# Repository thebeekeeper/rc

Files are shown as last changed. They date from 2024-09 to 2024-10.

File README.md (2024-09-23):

TURBO TORNADO
=============

When I was a kid I had a RC car that I really liked to play with, but it pretty rarely worked.  30+ years later I have a couple of decades of experience building embedded systems to control motors and stuff like that so I decided to design replacement electronics for it so my kid can play with it.

To start, I took the top off the car and removed the old PCB.  Here's what we see under there:

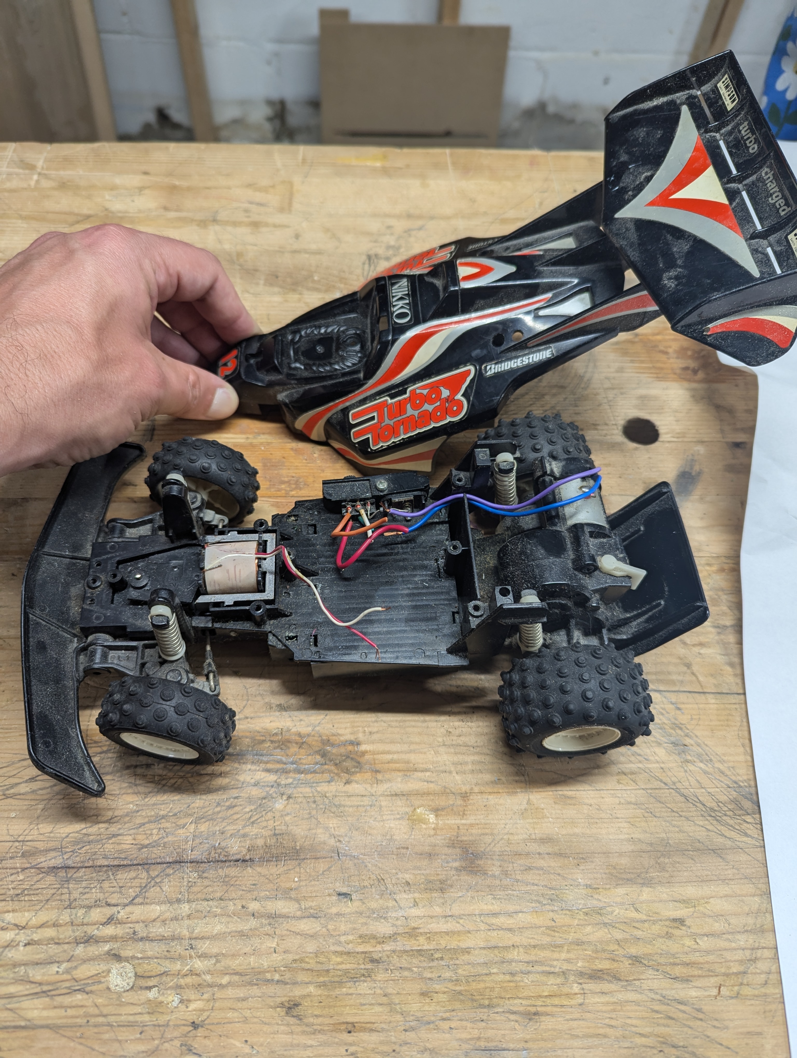
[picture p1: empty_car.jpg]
Empty Car


We've got leads to the coil that controls steering and some on the other end to the drive motor.  On the bottom there are 6 slots for AA batteries, so I'm assuming the motor and solenoid will work off 9V.  I checked this by connecting a 9V battery to both pairs of leads and saw that the steering and drive motor still work.  To change direction of both actuators, you can just reverse polarity on the battery.

What I really want to do with this project is put a camera where that guys head is supposed to be.  I've always wanted a first person view when driving the car around.

## Parts Selection

The features I'm designing for are:

1. Video streaming to some remote device
2. Wireless control
3. Ability to drive two inductive loads with PWM

I've been using `esp32` devices at work for a while, so I decided on the `ESP32-S3-MINI-1U-N8`.  I found the schematic for the `esp32-cam` board [here](https://github.com/SeeedDocument/forum_doc/blob/master/reg/ESP32_CAM_V1.6.pdf) and it looks pretty straightforward to wire to an FPC connector for a standard camera.  It also supports Bluetooth and WiFi, so I'll have some options for wireless control and video streaming.  I've read that it has issues with video quality when using the chip antenna, so I'll plan on using an external antenna.

To drive the motor and solenoid I was initially planning to build couple of standard H-bridge circuits, but then I found [A3909GLNTR](https://www.digikey.com/en/products/detail/allegro-microsystems/A3909GLNTR-T/3979655) which is an IC with the exact circuit I'd be building anyway so I decided to use that.  I've used some Allegro parts in other designs and they've worked well, so this should be pretty easy.

Got the rev0 boards back an assembled and the drive motor just whines and doesn't turn!  Tried adding some capacitance but that didn't really help.  I can't find any specs for the motor that's installed on the machine so I'm guessing the driver IC isn't able to source the stall current for the motor when it's connected to the gearbox.  I tested the driver with a motor I have lying around with no mechanical load on it and it worked fine.  The `A3909GLNTR` datasheet says you can parallel the outputs to get more current.  Tried that and it starts up the motor and runs no problem.  Added a second driver IC and updated the layout for a rev1 board.

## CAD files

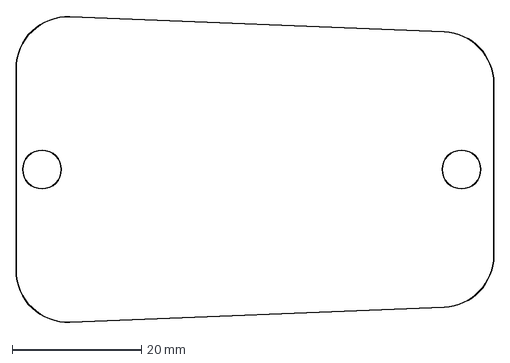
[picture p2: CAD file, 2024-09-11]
board/outline.dxf
74.0 x 47.5 mm

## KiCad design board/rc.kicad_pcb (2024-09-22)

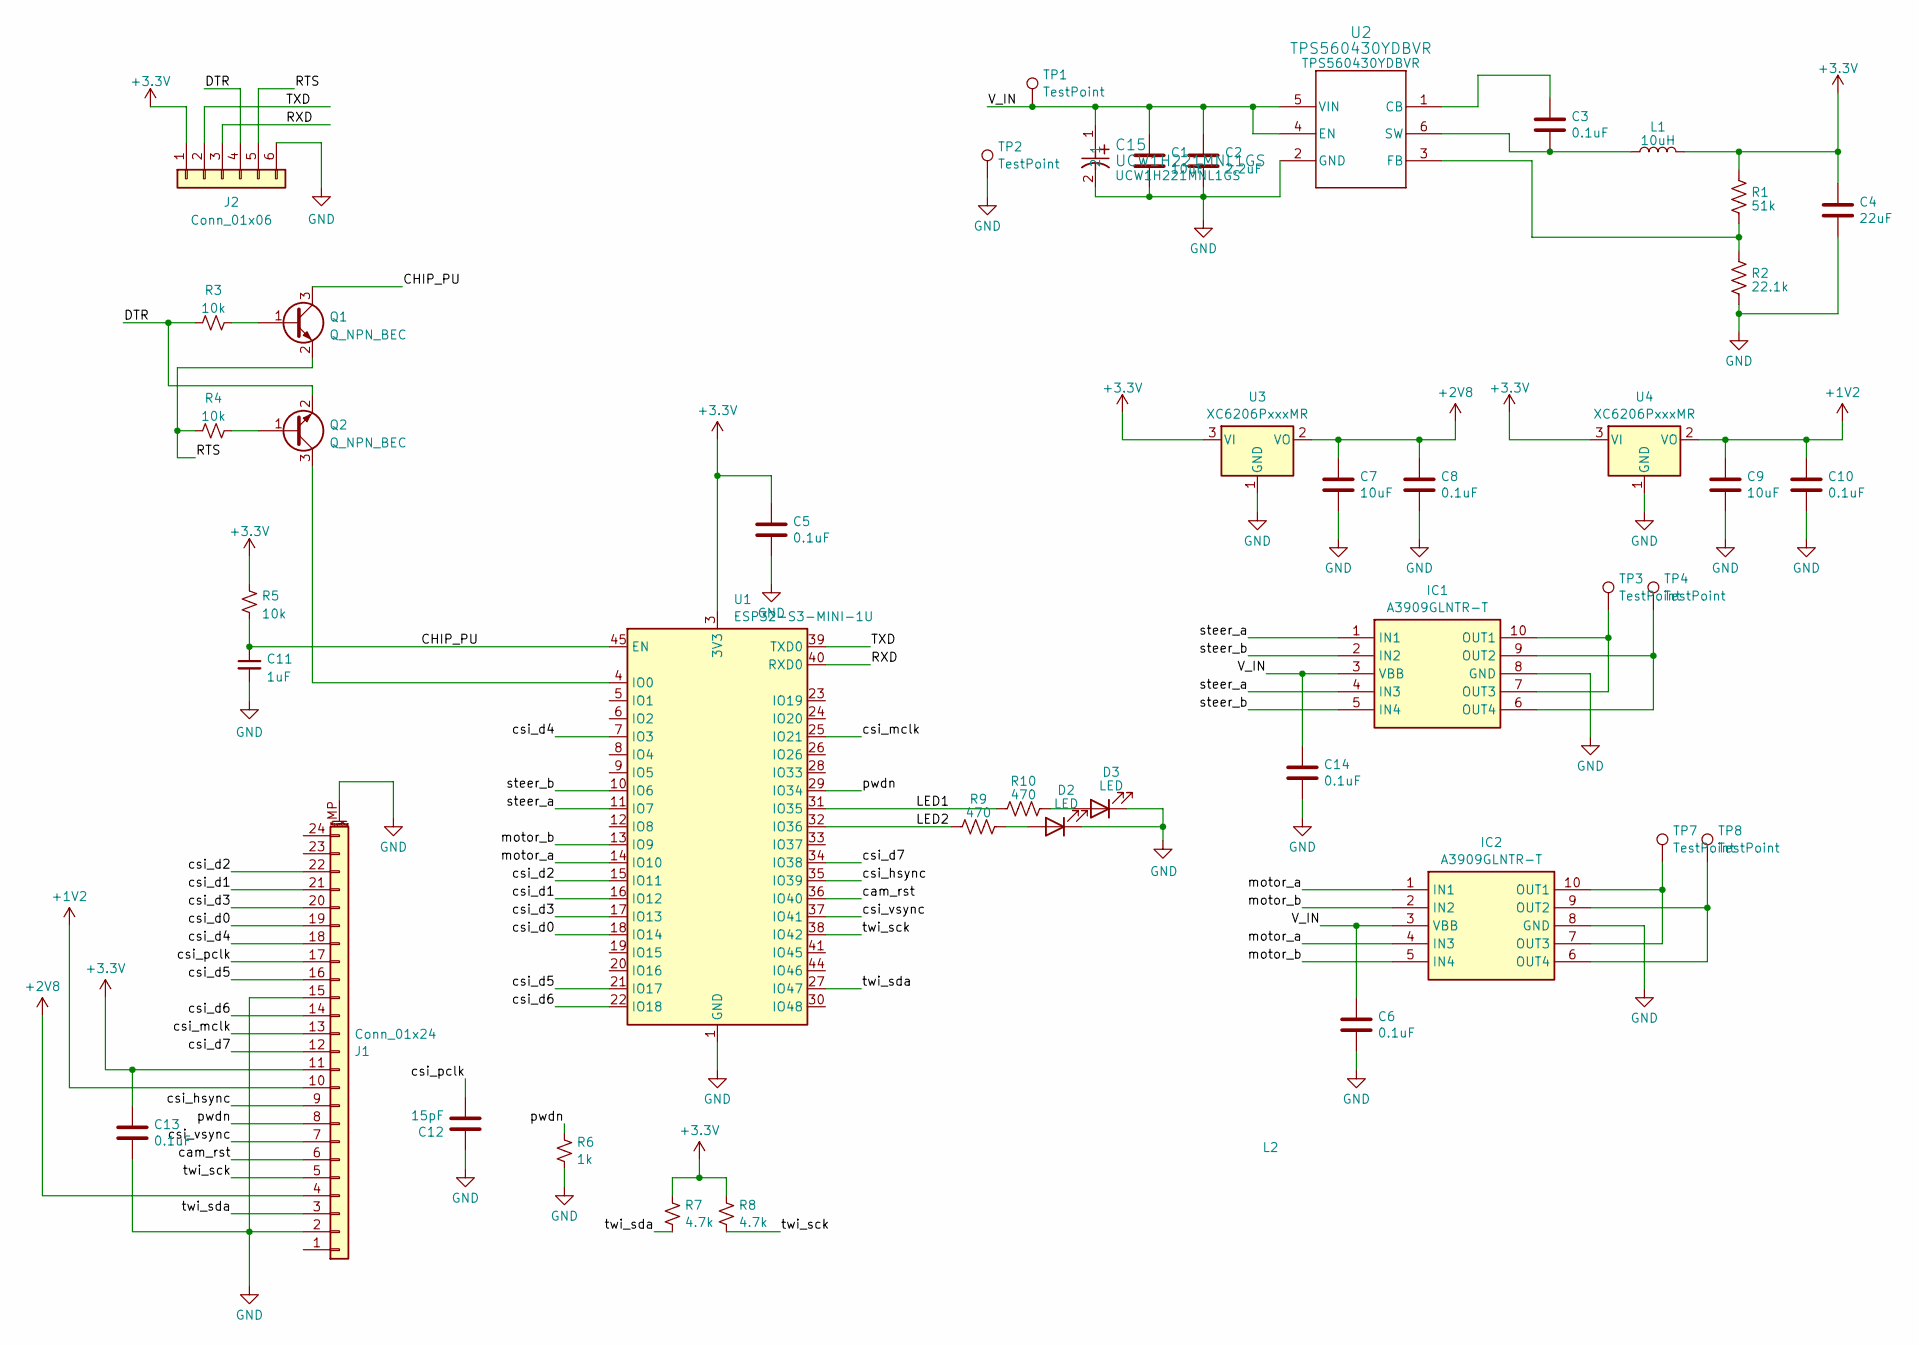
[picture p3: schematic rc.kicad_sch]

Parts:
C1: 10uF; C_1206_3216Metric; ManufacturerPartNumber C3216X5R1H106K160AB
C2: 2.2uF; C_0603_1608Metric; ManufacturerPartNumber GRM188R61H225KE11D
C3, C5, C6, C8, C10, C13, C14: 0.1uF; C_0603_1608Metric; ManufacturerPartNumber GRM188R71H104KA93D
C4: 22uF; C_0805_2012Metric; ManufacturerPartNumber C2012X5R1V226M125AC
C7, C9: 10uF; C_0603_1608Metric; ManufacturerPartNumber GRM188R71H104KA93D
C11: 1uF; C_0805_2012Metric; ManufacturerPartNumber CL21B105KOFNFNE
C12: 15pF; C_0603_1608Metric; ManufacturerPartNumber GRM188R71H104KA93D
C15: UCW1H221MNL1GS; ManufacturerPartNumber UCW1H221MNL1GS
D2, D3: LED; LED_0603_1608Metric; ManufacturerPartNumber B1911USD-20D000114U1930
IC1, IC2: A3909GLNTR-T; SOP100P600X175-10N; Mouser Part Number 250-A3909GLNTR-T
J1: Conn_01x24; Hirose_FH12-24S-0.5SH_1x24-1MP_P0.50mm_Horizontal
J2: Conn_01x06; PinHeader_1x06_P2.54mm_Vertical; ManufacturerPartNumber TSW-106-07-G-S
L1: 10uH; SRN3010C2R2M; ManufacturerPartNumber SRN3010C-100M
L2: bird
Q1, Q2: Q_NPN_BEC; SOT-23; ManufacturerPartNumber MMSS8050-H-TP
R1: 51k; R_0805_2012Metric; ManufacturerPartNumber RMCF0805JT51K0
R2: 22.1k; R_0805_2012Metric; ManufacturerPartNumber RMCF0805FT22K1
R3, R4, R5: 10k; R_0805_2012Metric; ManufacturerPartNumber RMCF0805FT10K0
R6: 1k; R_0805_2012Metric; ManufacturerPartNumber RMCF0805FT10K0
R7, R8: 4.7k; R_0805_2012Metric; ManufacturerPartNumber RMCF0805FT10K0
R9, R10: 470; R_0805_2012Metric; ManufacturerPartNumber RC0805FR-07470RL
TP1, TP2, TP3, TP4, TP7, TP8: TestPoint; MountingHole_2.2mm_M2_ISO7380_Pad_TopBottom
U1: ESP32-S3-MINI-1U; ESP32-S2-MINI-1U
U2: TPS560430YDBVR; DBV0006A_L; ManufacturerPartNumber TPS560430YDBVR
U3, U4: XC6206PxxxMR; SOT-23-3

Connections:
+1V2: C9.1, C10.1, J1.10, U4.2 (VO)
+2V8: C7.1, C8.1, J1.4, U3.2 (VO)
+3.3V: C4.1, C5.1, C13.1, J1.11, J2.1, L1.2, R1.2, R5.1, R7.2, R8.2, U1.3 (3V3), U3.3 (VI), U4.3 (VI)
/CHIP_PU: C11.1, Q1.3 (C), R5.2, U1.45 (EN)
/DTR: J2.4, Q2.2 (E), R3.1
/LED1: R10.1, U1.31 (IO35)
/LED2: R9.1, U1.32 (IO36)
/RTS: J2.5, Q1.2 (E), R4.1
/RXD: J2.3, U1.40 (RXD0)
/TXD: J2.2, U1.39 (TXD0)
/V_IN: C1.1, C2.1, C6.1, C14.1, C15.1, IC1.3 (VBB), IC2.3 (VBB), TP1.1, U2.4 (EN), U2.5 (VIN)
/cam_rst: J1.6, U1.36 (IO40)
/csi_d0: J1.19, U1.18 (IO14)
/csi_d1: J1.21, U1.16 (IO12)
/csi_d2: J1.22, U1.15 (IO11)
/csi_d3: J1.20, U1.17 (IO13)
/csi_d4: J1.18, U1.7 (IO3)
/csi_d5: J1.16, U1.21 (IO17)
/csi_d6: J1.14, U1.22 (IO18)
/csi_d7: J1.12, U1.34 (IO38)
/csi_hsync: J1.9, U1.35 (IO39)
/csi_mclk: J1.13, U1.25 (IO21)
/csi_pclk: C12.2, J1.17
/csi_vsync: J1.7, U1.37 (IO41)
/motor_a: IC2.1 (IN1), IC2.4 (IN3), U1.14 (IO10)
/motor_b: IC2.2 (IN2), IC2.5 (IN4), U1.13 (IO9)
/pwdn: J1.8, R6.2, U1.29 (IO34)
/steer_a: IC1.1 (IN1), IC1.4 (IN3), U1.11 (IO7)
/steer_b: IC1.2 (IN2), IC1.5 (IN4), U1.10 (IO6)
/twi_sck: J1.5, R8.1, U1.38 (IO42)
/twi_sda: J1.3, R7.1, U1.27 (IO47)
GND: C1.2, C2.2, C4.2, C5.2, C6.2, C7.2, C8.2, C9.2, C10.2, C11.2, C12.1, C13.2, C14.2, C15.2, D2.1 (K), D3.1 (K), IC1.8 (GND), IC2.8 (GND), J1.2, J1.15, J1.MP (MountPin), J2.6, R2.1, R6.1, TP2.1, U1.1 (GND), U1.2 (GND), U1.42 (GND), U1.43 (GND), U1.46 (GND), U1.47 (GND), U1.48 (GND), U1.49 (GND), U1.50 (GND), U1.51 (GND), U1.52 (GND), U1.53 (GND), U1.54 (GND), U1.55 (GND), U1.56 (GND), U1.57 (GND), U1.58 (GND), U1.59 (GND), U1.60 (GND), U1.61 (GND), U1.62 (GND), U1.63 (GND), U1.64 (GND), U1.65 (GND), U2.2 (GND), U3.1 (GND), U4.1 (GND)
unnamed: D2.2 (A), R9.2
unnamed: D3.2 (A), R10.2
unnamed: IC1.7 (OUT3), IC1.10 (OUT1), TP3.1
unnamed: IC1.6 (OUT4), IC1.9 (OUT2), TP4.1
unnamed: IC2.7 (OUT3), IC2.10 (OUT1), TP7.1
unnamed: IC2.6 (OUT4), IC2.9 (OUT2), TP8.1
unnamed: Q1.1 (B), R3.2
unnamed: Q2.1 (B), R4.2
unnamed: Q2.3 (C), U1.4 (IO0)
unnamed: C3.1, U2.1 (CB)
unnamed: R1.1, R2.2, U2.3 (FB)
unnamed: C3.2, L1.1, U2.6 (SW)

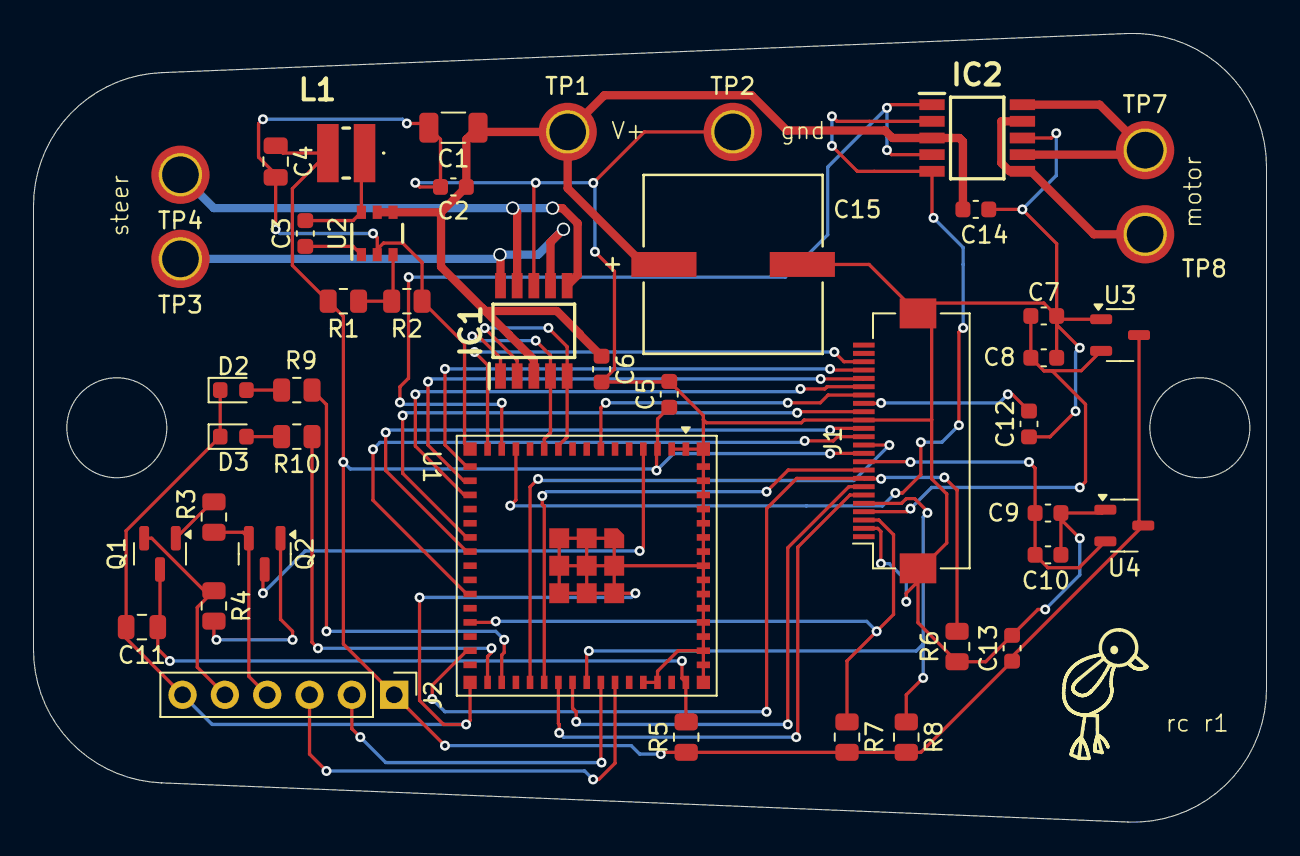
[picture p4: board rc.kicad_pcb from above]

Board: 2 copper layers, 74.0 x 47.3 mm, 45 parts (0 on the bottom side), 44 nets.

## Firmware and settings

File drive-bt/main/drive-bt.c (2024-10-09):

#include <stdio.h>
#include "sdkconfig.h"
#include "freertos/FreeRTOS.h"
#include "freertos/task.h"
#include "esp_system.h"
#include "esp_log.h"
#include "driver/gpio.h"
#include "driver/ledc.h"



#include "nimble/nimble_port.h"
#include "nimble/nimble_port_freertos.h"
#include "host/ble_hs.h"
#include "host/util/util.h"
#include "console/console.h"
#include "services/gap/ble_svc_gap.h"
#include "blecent.h"

#define PWM

#define TAG "drive-bt"

void init_io(void);

#define LED1 GPIO_NUM_35
#define LED2 GPIO_NUM_36

#define STEER_A GPIO_NUM_7
#define STEER_B GPIO_NUM_6
#define MOTOR_A GPIO_NUM_10
#define MOTOR_B GPIO_NUM_9

#define LEDC_TIMER LEDC_TIMER_0
#define LEDC_MODE LEDC_LOW_SPEED_MODE
//#define LEDC_OUTPUT_IO (MOTOR_A) // Define the output GPIO
//#define LEDC_OUTPUT_B (MOTOR_B)
#define MOTOR_A_CHANNEL LEDC_CHANNEL_0
#define MOTOR_B_CHANNEL LEDC_CHANNEL_1
#define STEER_A_CHANNEL LEDC_CHANNEL_2
#define STEER_B_CHANNEL LEDC_CHANNEL_3
#define LEDC_DUTY_RES LEDC_TIMER_13_BIT // Set duty resolution to 13 bits
//#define LEDC_DUTY (1096)                // Set duty to 50%. (2 ** 13) * 50% = 4096
#define LEDC_FREQUENCY (200)            // Frequency in Hertz. Set frequency at 4 kHz

// called from the BLE handler
void update_outputs(int8_t drive, int8_t steer) {
    uint32_t dc = 0;
    if(drive > 10) {
        dc = drive * 53; 
        ESP_LOGI(TAG, "setting drive dc forward: %lu", dc);
        ESP_ERROR_CHECK(ledc_set_duty(LEDC_MODE, MOTOR_A_CHANNEL, dc));
        ESP_ERROR_CHECK(ledc_update_duty(LEDC_MODE, MOTOR_A_CHANNEL));
        // turn off channel B
        ESP_ERROR_CHECK(ledc_set_duty(LEDC_MODE, MOTOR_B_CHANNEL, 0));
        ESP_ERROR_CHECK(ledc_update_duty(LEDC_MODE, MOTOR_B_CHANNEL));
    }
    else if(drive < -10) {
        dc = drive * -53; 
        ESP_LOGI(TAG, "setting drive dc reverse: %lu", dc);
        ESP_ERROR_CHECK(ledc_set_duty(LEDC_MODE, MOTOR_A_CHANNEL, 0));
        ESP_ERROR_CHECK(ledc_update_duty(LEDC_MODE, MOTOR_A_CHANNEL));
        ESP_ERROR_CHECK(ledc_set_duty(LEDC_MODE, MOTOR_B_CHANNEL, dc));
        ESP_ERROR_CHECK(ledc_update_duty(LEDC_MODE, MOTOR_B_CHANNEL));
    }
    else {
        dc = 0;
        ESP_ERROR_CHECK(ledc_set_duty(LEDC_MODE, MOTOR_A_CHANNEL, dc));
        ESP_ERROR_CHECK(ledc_update_duty(LEDC_MODE, MOTOR_A_CHANNEL));
        ESP_ERROR_CHECK(ledc_set_duty(LEDC_MODE, MOTOR_B_CHANNEL, dc));
        ESP_ERROR_CHECK(ledc_update_duty(LEDC_MODE, MOTOR_B_CHANNEL));
    }

    if(steer > 10) {
        //dc = 3000 + (steer * 53); 
        dc = 8192;
        ESP_LOGI(TAG, "setting steer left: %lu", dc);
        ESP_ERROR_CHECK(ledc_set_duty(LEDC_MODE, STEER_A_CHANNEL, dc));
        ESP_ERROR_CHECK(ledc_update_duty(LEDC_MODE, STEER_A_CHANNEL));
        // turn off channel B
        ESP_ERROR_CHECK(ledc_set_duty(LEDC_MODE, STEER_B_CHANNEL, 0));
        ESP_ERROR_CHECK(ledc_update_duty(LEDC_MODE, STEER_B_CHANNEL));
    }
    else if(steer < -10) {
        //dc = steer * 53; 
        dc = 8192;
        ESP_LOGI(TAG, "setting steer right: %lu", dc);
        ESP_ERROR_CHECK(ledc_set_duty(LEDC_MODE, STEER_A_CHANNEL, 0));
        ESP_ERROR_CHECK(ledc_update_duty(LEDC_MODE, STEER_A_CHANNEL));
        ESP_ERROR_CHECK(ledc_set_duty(LEDC_MODE, STEER_B_CHANNEL, dc));
        ESP_ERROR_CHECK(ledc_update_duty(LEDC_MODE, STEER_B_CHANNEL));
    }
    else {
        dc = 0;
        ESP_ERROR_CHECK(ledc_set_duty(LEDC_MODE, STEER_A_CHANNEL, dc));
        ESP_ERROR_CHECK(ledc_update_duty(LEDC_MODE, STEER_A_CHANNEL));
        ESP_ERROR_CHECK(ledc_set_duty(LEDC_MODE, STEER_B_CHANNEL, dc));
        ESP_ERROR_CHECK(ledc_update_duty(LEDC_MODE, STEER_B_CHANNEL));
    }
}


static void example_ledc_init(void)
{
    // Prepare and then apply the LEDC PWM timer configuration
    ledc_timer_config_t ledc_timer = {
        .speed_mode = LEDC_MODE,
        .duty_resolution = LEDC_DUTY_RES,
        .timer_num = LEDC_TIMER,
        .freq_hz = LEDC_FREQUENCY, // Set output frequency at 4 kHz
        .clk_cfg = LEDC_AUTO_CLK};
    ESP_ERROR_CHECK(ledc_timer_config(&ledc_timer));

    // Prepare and then apply the LEDC PWM channel configuration
    ledc_channel_config_t ledc_channel = {
        .speed_mode = LEDC_MODE,
        .channel = MOTOR_A_CHANNEL,
        .timer_sel = LEDC_TIMER,
        .intr_type = LEDC_INTR_DISABLE,
        .gpio_num = MOTOR_A,
        .duty = 0, // Set duty to 0%
        .hpoint = 0};
    ESP_ERROR_CHECK(ledc_channel_config(&ledc_channel));

    ledc_channel_config_t ledc_channel_b = {
        .speed_mode = LEDC_MODE,
        .channel = MOTOR_B_CHANNEL,
        .timer_sel = LEDC_TIMER,
        .intr_type = LEDC_INTR_DISABLE,
        .gpio_num = MOTOR_B,
        .duty = 0, // Set duty to 0%
        .hpoint = 0};
    ESP_ERROR_CHECK(ledc_channel_config(&ledc_channel_b));

    ledc_channel_config_t ledc_channel_c = {
        .speed_mode = LEDC_MODE,
        .channel = STEER_A_CHANNEL,
        .timer_sel = LEDC_TIMER,
        .intr_type = LEDC_INTR_DISABLE,
        .gpio_num = STEER_A,
        .duty = 0, // Set duty to 0%
        .hpoint = 0};
    ESP_ERROR_CHECK(ledc_channel_config(&ledc_channel_c));

    ledc_channel_config_t ledc_channel_d = {
        .speed_mode = LEDC_MODE,
        .channel = STEER_B_CHANNEL,
        .timer_sel = LEDC_TIMER,
        .intr_type = LEDC_INTR_DISABLE,
        .gpio_num = STEER_B,
        .duty = 0, // Set duty to 0%
        .hpoint = 0};
    ESP_ERROR_CHECK(ledc_channel_config(&ledc_channel_d));
}

void app_main(void)
{
    ESP_LOGI(TAG, "hello");
    init_io();

    uint8_t led = 1;
    //gpio_set_level(MOTOR_A, 0);
    //gpio_set_level(MOTOR_B, 0);

    //gpio_set_level(STEER_A, 0);
    //gpio_set_level(STEER_B, 0);

#ifdef PWM
    // Set the LEDC peripheral configuration
    example_ledc_init();
    init_ble();
#endif

    while (1)
    {
        gpio_set_level(LED1, led);
        gpio_set_level(LED2, !led);
        // useful for testing hardware
#ifndef PWM
        gpio_set_level(STEER_A, led);
        gpio_set_level(STEER_B, !led);
        gpio_set_level(MOTOR_A, led);
        gpio_set_level(MOTOR_B, !led);
#endif
        led = !led;
        vTaskDelay(1000 / portTICK_PERIOD_MS);
    }
}

void init_io(void)
{
    gpio_config_t io_conf = {};
    io_conf.intr_type = GPIO_INTR_DISABLE;
    io_conf.mode = GPIO_MODE_OUTPUT;
    io_conf.pin_bit_mask = (1ULL << LED1);
    io_conf.pull_down_en = 0;
    io_conf.pull_up_en = 0;
    gpio_config(&io_conf);
    io_conf.pin_bit_mask = (1ULL << LED2);
    gpio_config(&io_conf);
#ifndef PWM
    io_conf.pin_bit_mask = (1ULL << STEER_A);
    gpio_config(&io_conf);
    io_conf.pin_bit_mask = (1ULL << STEER_B);
    gpio_config(&io_conf);
    io_conf.pin_bit_mask = (1ULL << MOTOR_A);
    gpio_config(&io_conf);
    io_conf.pin_bit_mask = (1ULL << MOTOR_B);
    gpio_config(&io_conf);
#endif
}

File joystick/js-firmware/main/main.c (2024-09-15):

#define I2C_ADC

#include <stdio.h>
#include "sdkconfig.h"
#include "freertos/FreeRTOS.h"
#include "freertos/task.h"
#include "esp_system.h"
#include "nvs_flash.h"
#include "nvs.h"
#include "driver/i2c.h"
#include "nimble.h"
#include "esp_log.h"
#include "esp_err.h"
#include "driver/gpio.h"
#include "js_data.h"

#define TAG "js"

#define GPIO_LED_1 7
#define GPIO_LED_2 10

#define GPIO_INPUT_BUTTON_1 18
#define GPIO_INPUT_BUTTON_2 19
#define GPIO_INPUT_PIN_SEL (1ULL << GPIO_INPUT_BUTTON_1)
#define GPIO_INPUT_PIN2_SEL (1ULL << GPIO_INPUT_BUTTON_2)

#define SDA_PIN 3
#define SCL_PIN 4
#define I2C_MASTER_TX_BUF_DISABLE 0 /*!< I2C master doesn't need buffer */
#define I2C_MASTER_RX_BUF_DISABLE 0 /*!< I2C master doesn't need buffer */
#define I2C_MASTER_TIMEOUT_MS       1000
#define ADC_ADDR 0x33
#define N_CHANNELS 5
#define VOLT_SCALE 0.000500122

js_reading js;

static int i2c_port = 0;
void init_adc(void)
{
        i2c_config_t conf = {
        .mode = I2C_MODE_MASTER,
        .sda_io_num = SDA_PIN,
        .sda_pullup_en = GPIO_PULLUP_DISABLE,
        .scl_io_num = SCL_PIN,
        .scl_pullup_en = GPIO_PULLUP_DISABLE,
        .master.clk_speed = 400000, // select frequency specific to your project
        .clk_flags = 0,
    };

    ESP_ERROR_CHECK(i2c_param_config(i2c_port, &conf));
    ESP_ERROR_CHECK(i2c_driver_install(i2c_port, I2C_MODE_MASTER, I2C_MASTER_RX_BUF_DISABLE, I2C_MASTER_TX_BUF_DISABLE, 0));

    // --F = setup byte, SEL[2..0] = internal reference, ref output, always on--
    // --2 = internal clock, unipolar, dont reset, dc--
    // D = SEL[2..0] = internal, not connected, always on
    // A = external clock (SCL), unipolar, don't reset, dontcare
    //uint8_t data = 0xDA;
    // r1 has an external reference hooked up - SEL = 0b010
    // setup byte
    uint8_t data = 0xAA;
    ESP_ERROR_CHECK(i2c_master_write_to_device(i2c_port, ADC_ADDR, &data, 1, I2C_MASTER_TIMEOUT_MS / portTICK_PERIOD_MS));
    data = 0b00001001;
    ESP_ERROR_CHECK(i2c_master_write_to_device(i2c_port, ADC_ADDR, &data, 1, I2C_MASTER_TIMEOUT_MS / portTICK_PERIOD_MS));

}
void read_joysticks(js_reading *js)
{
    uint8_t configByte = 0b00000001 | ((N_CHANNELS - 1) << 1);
    size_t i;
    uint8_t data[N_CHANNELS * 2];
    uint16_t reading = 0;
    uint16_t readings[N_CHANNELS] = { 0 };

    // writes config during the same operation as reading all input channels
    i2c_master_write_read_device(i2c_port, ADC_ADDR, &configByte, 1, &data[0], N_CHANNELS * 2, I2C_MASTER_TIMEOUT_MS / portTICK_PERIOD_MS);

    for (i = 0; i < N_CHANNELS; i++)
    {
        reading = (((uint16_t)(data[2 * i] & 0x0F)) << 8) | data[(2 * i) + 1];
        //printf("reading %i: %u\n", i, reading);
        // printf("%zu - %u\n", i, last_raw_value[i]);
        //float volts = (float)reading * VOLT_SCALE;
        //pressures[i] = (volts - V_MIN) * PSI_SCALE;
        readings[i] = reading;
        //ESP_LOGI(TAG, "value %i: %f", i, volts);
    }
    js->left_horizontal = (int8_t)((readings[4] - 2054) / 20);
    js->left_vertical = (int8_t)((readings[2] - 1984) / 19);
    js->right_horizontal = -1 * ((int8_t)((readings[1] - 2048) / 20));
    // this one isn't really working, think i bent a lead
    js->right_vertical = (int8_t)(readings[0]);

    //printf("%u\t%u\t%u\t%u\t%u\n", readings[0], readings[1], readings[2], readings[3], readings[4]);
}

void init_io(void)
{
    gpio_config_t io_conf = {};
    io_conf.intr_type = GPIO_INTR_DISABLE;
    io_conf.mode = GPIO_MODE_INPUT;
    io_conf.pin_bit_mask = GPIO_INPUT_PIN_SEL;
    io_conf.pull_down_en = 0;
    io_conf.pull_up_en = 1;
    gpio_config(&io_conf);

    io_conf.pin_bit_mask = GPIO_INPUT_PIN2_SEL;
    gpio_config(&io_conf);

    // set up LEDs
    io_conf.mode = GPIO_MODE_OUTPUT;
    io_conf.pin_bit_mask = (1uLL << GPIO_LED_1);
    io_conf.pull_up_en = 0;
    gpio_config(&io_conf);
    io_conf.pin_bit_mask = (1uLL << GPIO_LED_2);
    gpio_config(&io_conf);
}

void app_main(void)
{
    /* Initialize NVS — it is used to store PHY calibration data */
    esp_err_t ret = nvs_flash_init();
    if (ret == ESP_ERR_NVS_NO_FREE_PAGES || ret == ESP_ERR_NVS_NEW_VERSION_FOUND)
    {
        ESP_ERROR_CHECK(nvs_flash_erase());
        ret = nvs_flash_init();
    }
    ESP_ERROR_CHECK(ret);

    init_io();
    init_adc();
    startBLE();
    uint8_t led = 0;

    xTaskCreate(vTasksendNotification, "vTasksendNotification", 4096, NULL, 1, &xHandle);

    while (true)
    {
        read_joysticks(&js);
        ESP_LOGI(TAG, "drive: %i\tturn: %i", js.left_vertical, js.right_horizontal);
        led++;
        if(led == 1) {
         gpio_set_level(GPIO_LED_1, 1);
        } else {
            gpio_set_level(GPIO_LED_1, 0);
        }
        if(led > 5) {
            led = 0;
        }
    
        vTaskDelay(500 / portTICK_PERIOD_MS);
    }
}

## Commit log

2024-09-11 initial pcb design
    [outline.dxf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]
2024-09-11 Added readme
    [outline.dxf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]
2024-09-22 added another motor driver, made mounting holes smaller, added cap for input voltage
    [rc-B_Cu.gbr, rc-B_Mask.gbr, rc-B_Paste.gbr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]
2024-10-06 can control drive motor from BT joystick
2024-10-09 set up pwm for motor and steering outputs
2024-10-09 fixed some logic bugs with the motor control
    [drive-bt.c]
